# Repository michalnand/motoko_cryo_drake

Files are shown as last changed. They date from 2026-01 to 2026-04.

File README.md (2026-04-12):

# motoko cryo drake - line following robot

robot photos

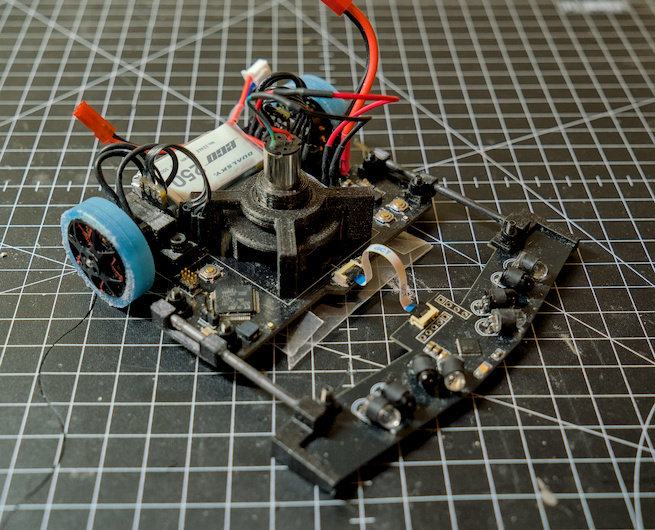
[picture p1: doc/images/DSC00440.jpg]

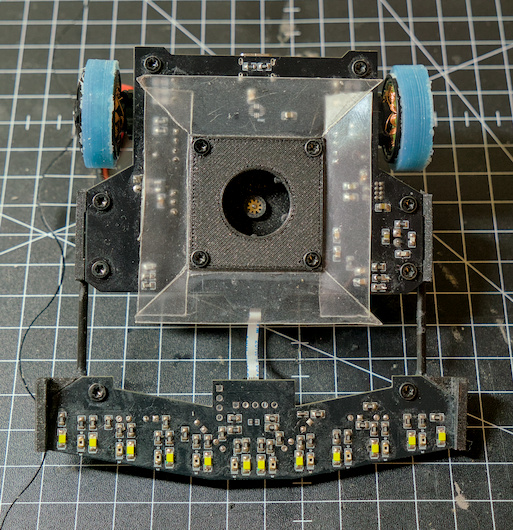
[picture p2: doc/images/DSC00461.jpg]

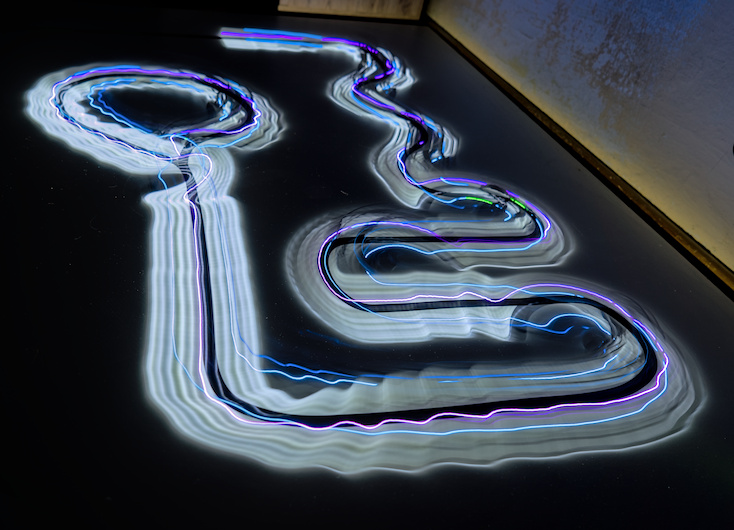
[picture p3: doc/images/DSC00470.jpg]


# hardware

- main MCU stm32f722, cortex m7, 216MHz, FPU
- sensors MCU stm32g031, cortex m0, 64MHz
- BLDC motors, custom windings, custom silicone tires
- 3 phase drivers, 2 x MP6541, 8A drivers
- turbine - some random DC drone motor + 3D print
- line sensors : 10x phototransistor + white LED
- obstacle sensors : 4x IR photo diode
- power 2D LiPo, Dualsky 250mAh
- USB C, debug connectors, RGB leds

# robot PCB

4 layer pcb, designed in EasyEDA

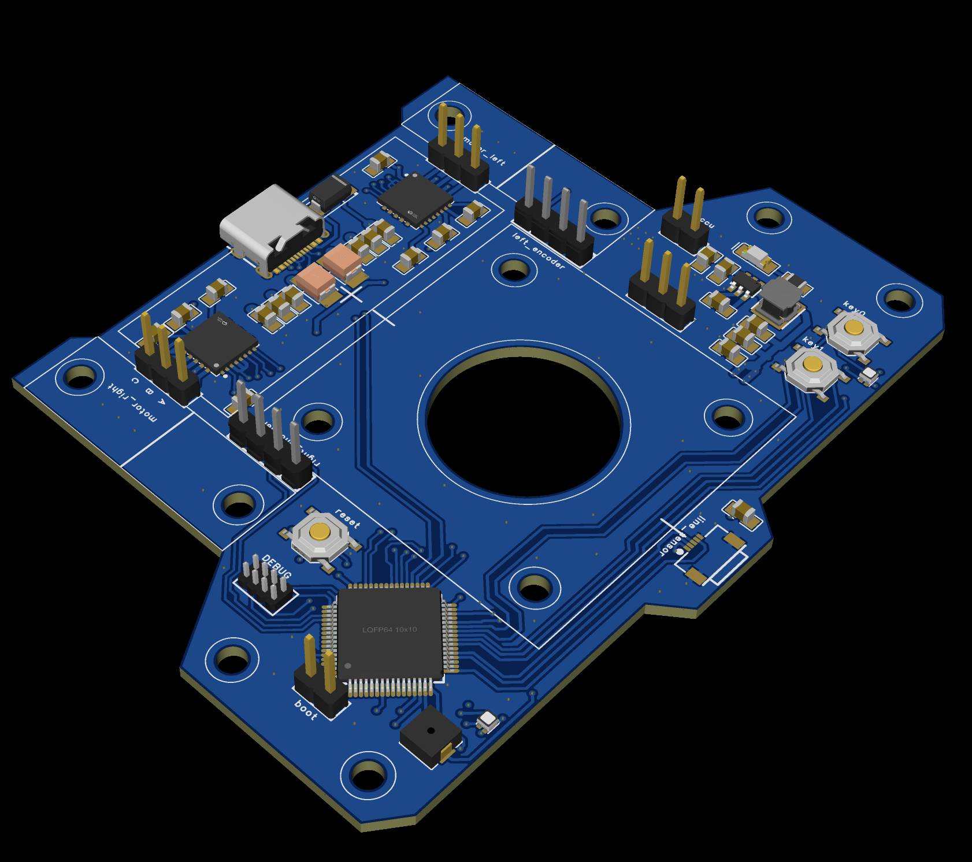
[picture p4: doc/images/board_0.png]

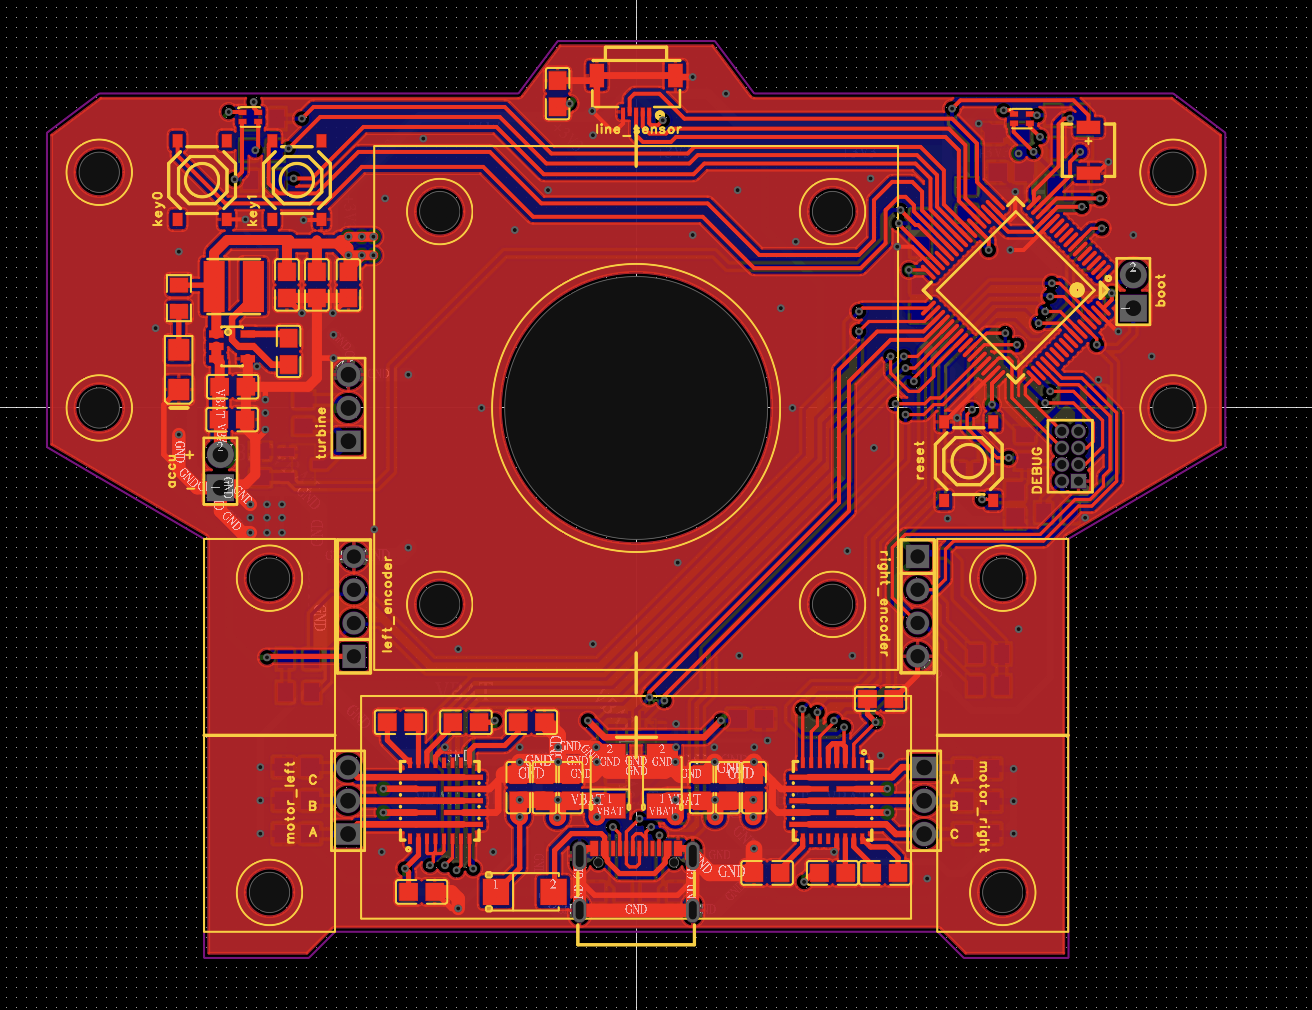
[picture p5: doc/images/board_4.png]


# software 

inner loop, 2kHz : 
- FOC control for BLDC motors
- kalman filter state estimator

outer loop
- analytical MPC
- constrained path planner
- koopman operator non linear controller

# block diagram

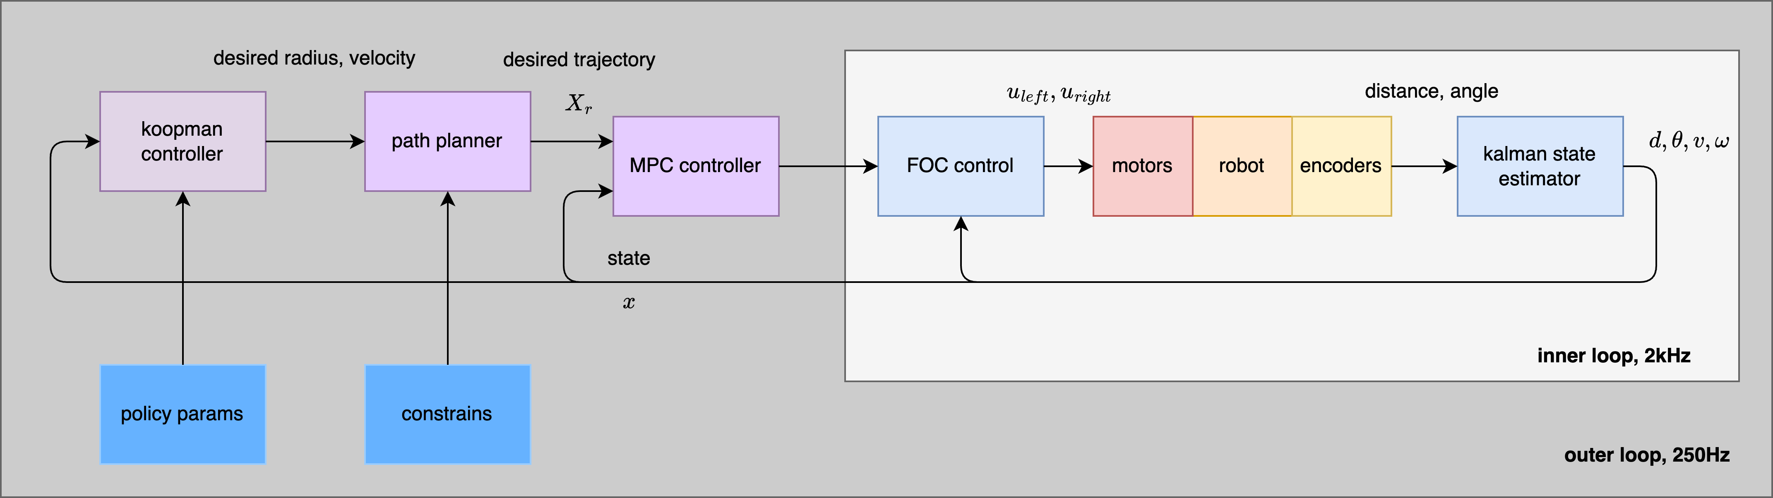
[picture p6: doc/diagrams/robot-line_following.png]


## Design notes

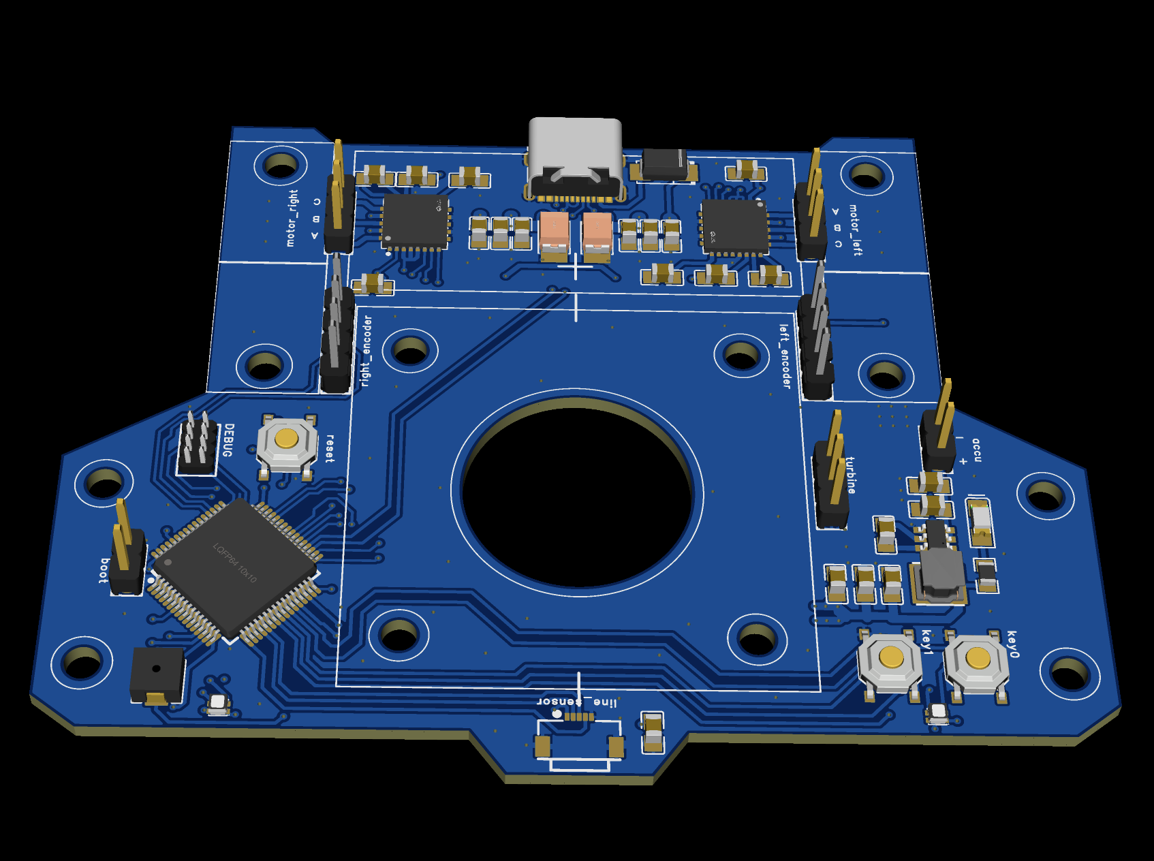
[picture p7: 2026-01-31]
doc/images/board_1.png

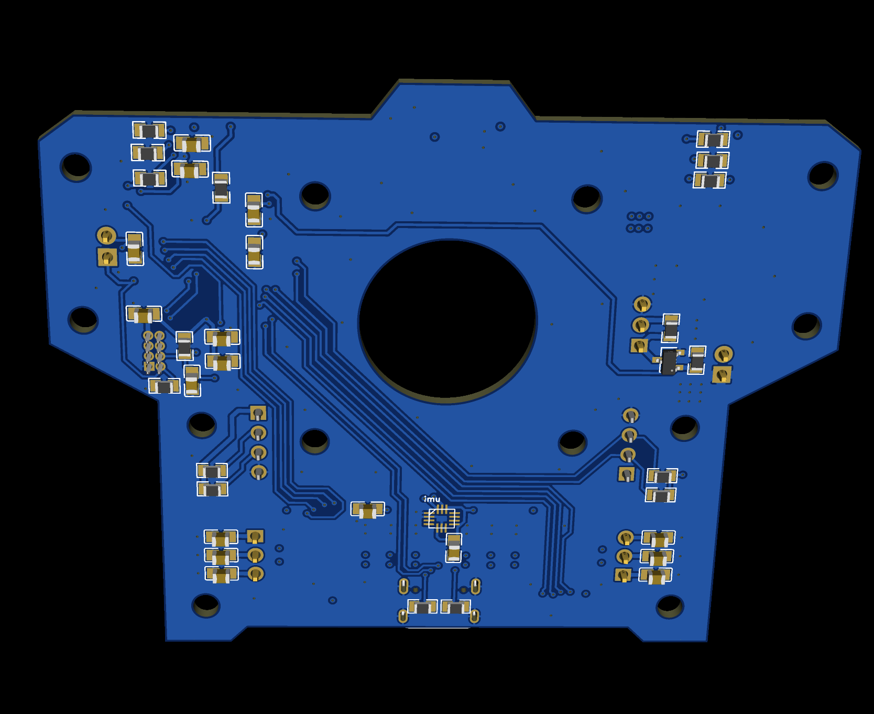
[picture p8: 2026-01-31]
doc/images/board_3.png

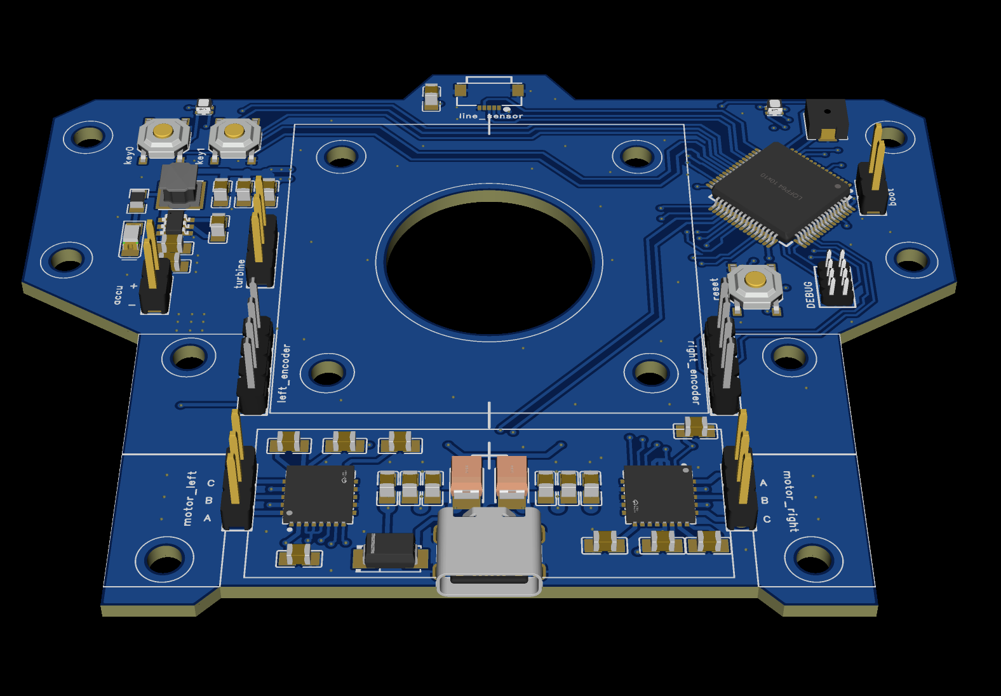
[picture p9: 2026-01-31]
doc/images/board_2.png

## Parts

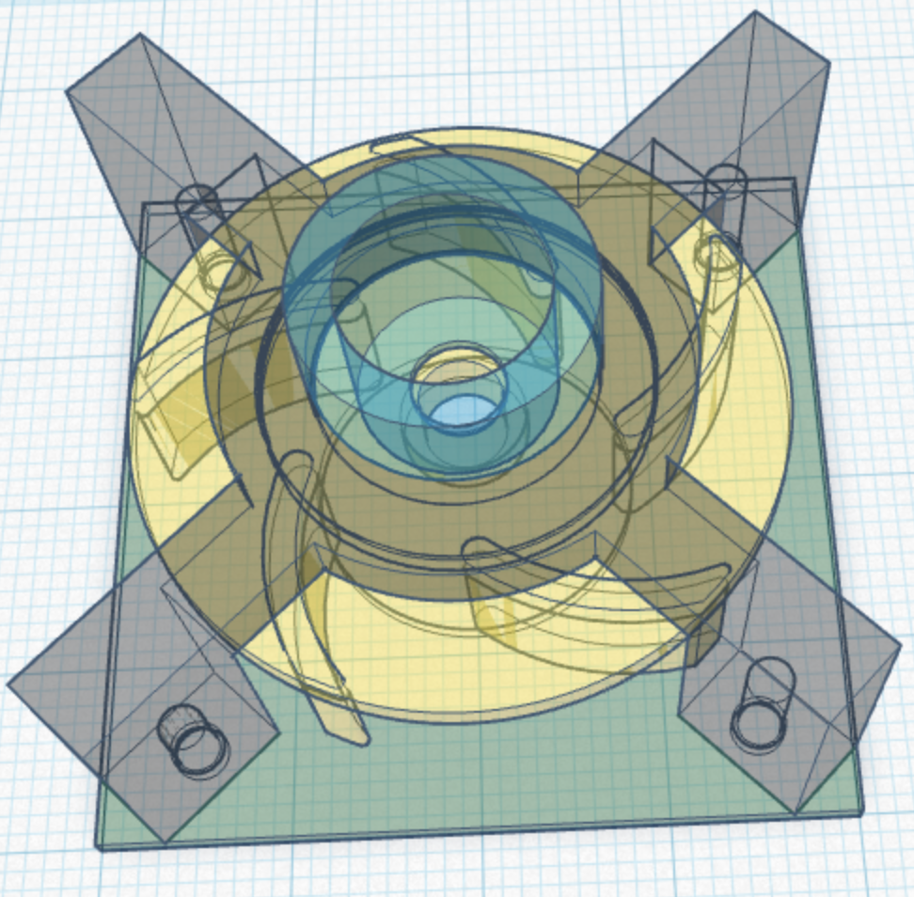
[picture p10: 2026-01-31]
3d_parts/images/turbofan.png

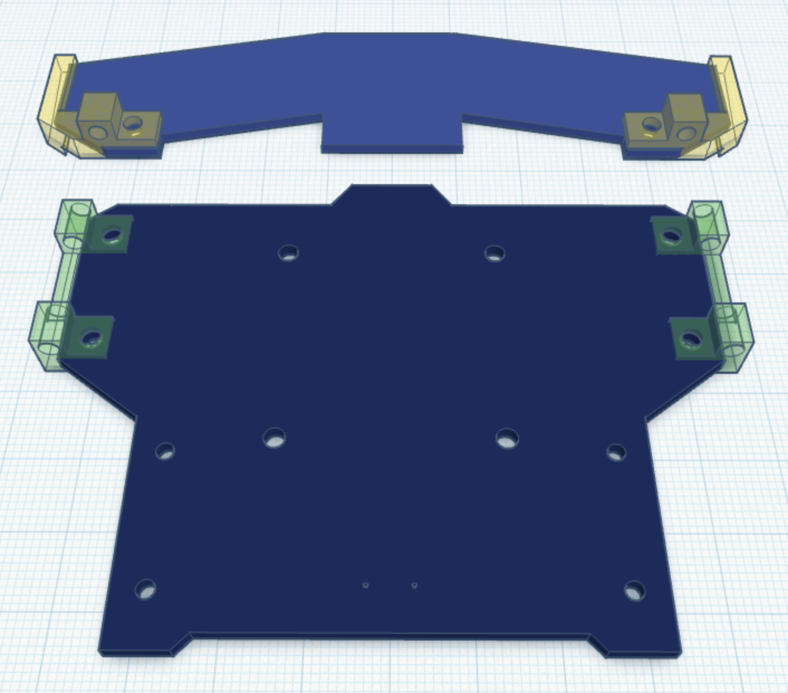
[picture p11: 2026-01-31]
3d_parts/images/sensor_holder_b.png

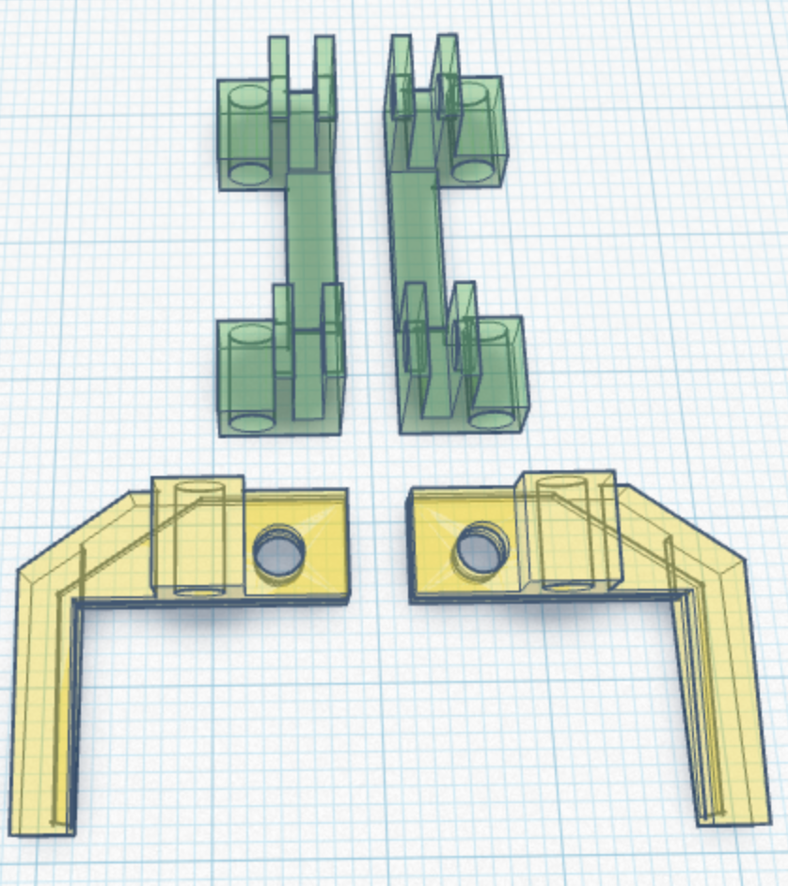
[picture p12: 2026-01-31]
3d_parts/images/sensor_holder_a.png

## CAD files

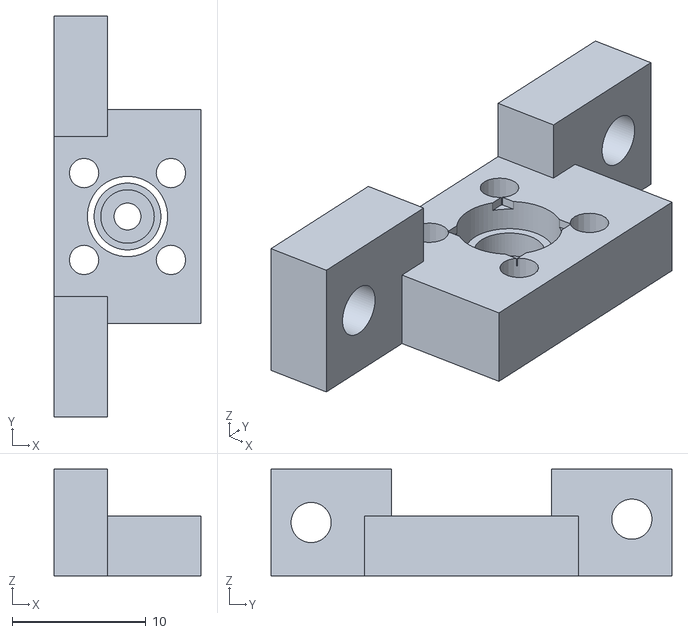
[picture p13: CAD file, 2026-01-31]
3d_parts/motors_bracket/motor_holder_1404.stl
11.0 x 30.0 x 8.00

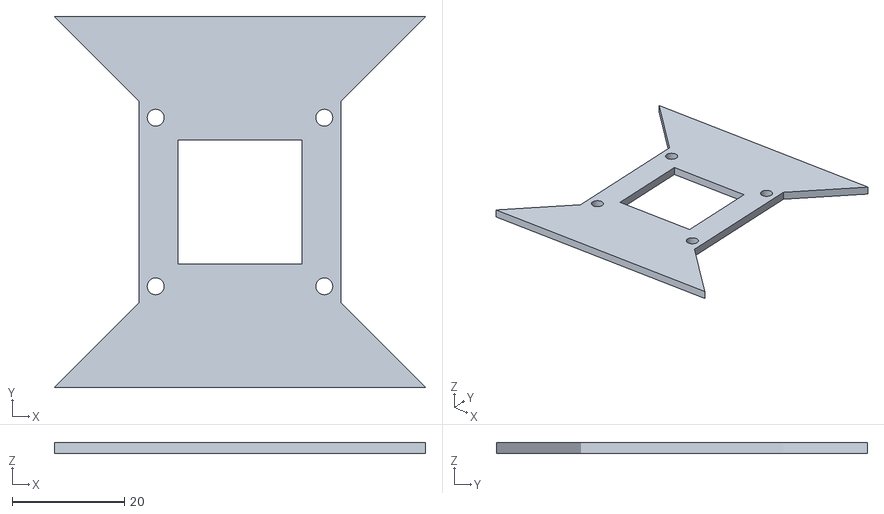
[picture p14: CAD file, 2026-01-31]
3d_parts/sealing_cut_jig/sealing_a.stl
66.0 x 66.0 x 2.00

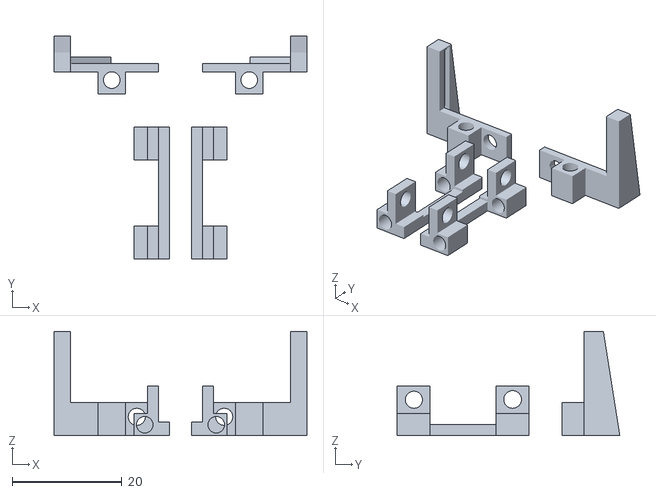
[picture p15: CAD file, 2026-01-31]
3d_parts/sensors/sensor_holder.stl
46.0 x 40.5 x 19.0

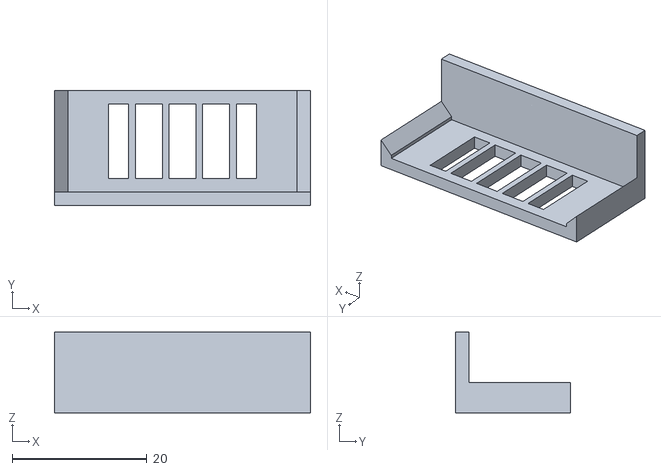
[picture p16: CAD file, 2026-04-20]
3d_parts/turbofan/turbo_fan_guard.stl
38.0 x 17.0 x 12.0

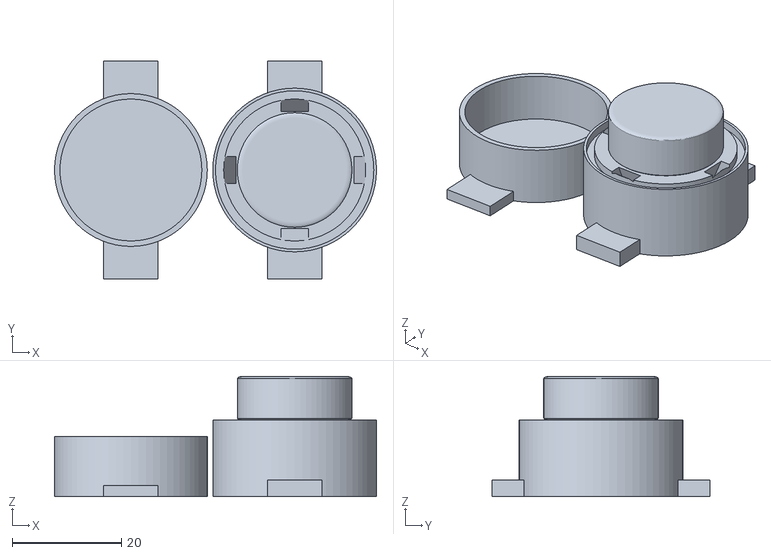
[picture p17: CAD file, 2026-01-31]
3d_parts/wheel_tire_silicone_form/whell_tire_form_b.stl
59.0 x 40.0 x 22.0

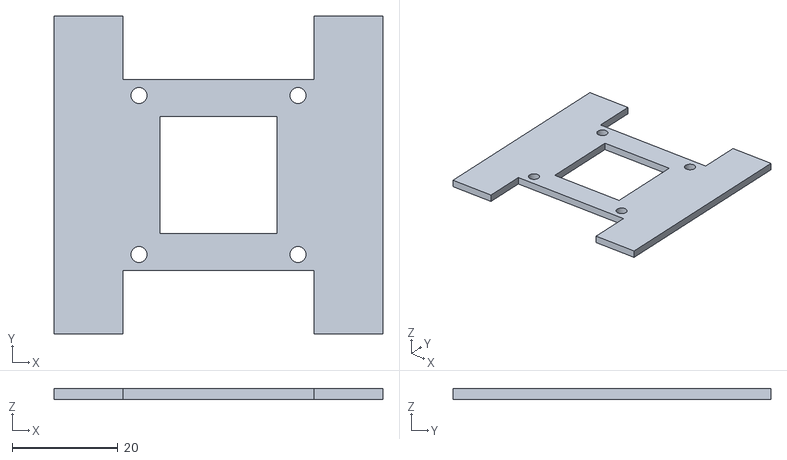
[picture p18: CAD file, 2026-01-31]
3d_parts/sealing_cut_jig/sealing_b.stl
62.0 x 60.0 x 2.00

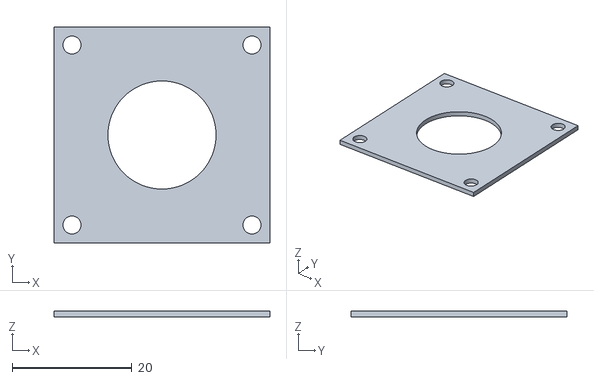
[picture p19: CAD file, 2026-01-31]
3d_parts/turbofan/turbofan_d.stl
36.0 x 36.0 x 1.00

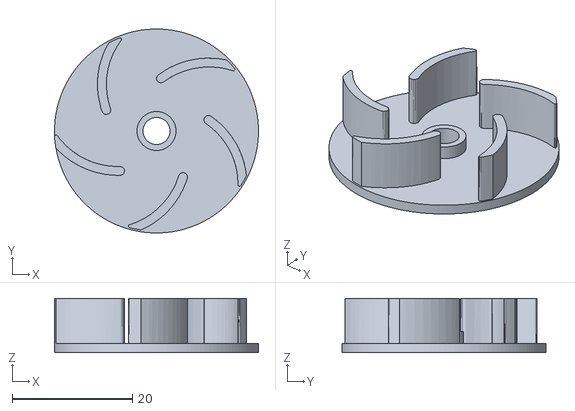
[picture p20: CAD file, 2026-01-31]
3d_parts/turbofan/turbofan_a.stl
34.0 x 34.0 x 9.01

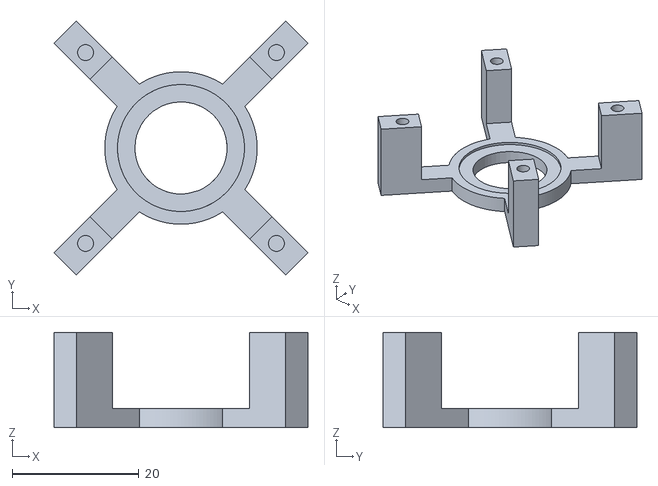
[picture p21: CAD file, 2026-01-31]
3d_parts/turbofan/turbofan_b.stl
40.0 x 40.0 x 15.0

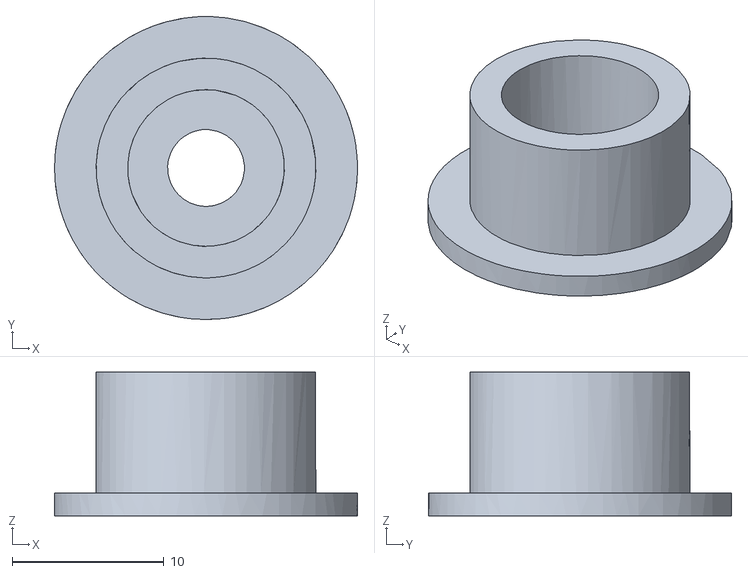
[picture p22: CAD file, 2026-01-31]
3d_parts/turbofan/turbofan_c.stl
20.0 x 20.0 x 9.50

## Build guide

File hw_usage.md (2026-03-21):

# STM32F722 Hardware Pin & Peripheral Usage

## Timers

| Timer / Source | Function | Frequency |
|---|---|---|
| SysTick | Timer, delays, basic timing | 1000 Hz |
| TIM7 (`TIM7_IRQHandler`) | Motor FOC control loop (incl. I2C encoder read) | 2000 Hz |
| TIM8/TIM13 (`TIM8_UP_TIM13_IRQHandler`) | Sensor sampling (line sensor, proximity) | 200 – 400 Hz |

---

## Turbine Fan PWM

| Signal | Pin  | Peripheral |
|---|---|---|
| PWM | PB10 | TIM2_CH3 |

---

## Left Motor – 3-Phase BLDC PWM (TIM3)

| Signal | Pin | Peripheral |
|---|-----|---|
| PWMA | PC6 | TIM3_CH1 |
| PWMB | PC7 | TIM3_CH2 |
| PWMC | PC8 | TIM3_CH3 |
| Enable | PC9 | GPIO |

## Right Motor – 3-Phase BLDC PWM (TIM4)

| Signal | Pin | Peripheral |
|---|-----|---|
| PWMA | PB6 | TIM4_CH1 |
| PWMB | PB7 | TIM4_CH2 |
| PWMC | PB8 | TIM4_CH3 |
| Enable | PB9 | GPIO |

---

## Motor Encoders (I2C, bit-bang)

| Encoder | SDA  | SCL  |
|---|---|---|
| Left encoder  | PC11 | PC10 |
| Right encoder | PB5  | PC12 |

---

## Line Sensor

| Signal | Pin | Type |
|---|-----|---|
| SDA | PA5 | I2C  |
| SCL | PA4 | I2C  |
| Reset  | PA3 | GPIO |

---

## Keys

| Key  | Pin |
|---|-----|
| KEY0 | PB2 |
| KEY1 | PB1 |

## RGB LEDs (active low)

| LED | R | G | B |
|---|-----|-----|-----|
| LED A | PB0 | PC4 | PA7 |
| LED B | PA0 | PA1 | PA2 |

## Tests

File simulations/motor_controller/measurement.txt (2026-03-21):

machine ready
u_in   =  0.200
k      =  321.474
rpm    = 613
x_mean =  64.294
x_var  =  48.687

u_in   =  0.300
k      =  273.746
rpm    = 784
x_mean =  82.124
x_var  =  78.852

u_in   =  0.400
k      =  230.747
rpm    = 881
x_mean =  92.298
x_var  =  145.622

u_in   =  0.500
k      =  198.342
rpm    = 947
x_mean =  99.171
x_var  =  108.676

u_in   =  0.600
k      =  175.433
rpm    = 1005
x_mean =  105.260
x_var  =  137.009

u_in   =  0.700
k      =  154.284
rpm    = 1031
x_mean =  107.999
x_var  =  169.827

u_in   =  0.800
k      =  139.777
rpm    = 1067
x_mean =  111.822
x_var  =  171.886

u_in   =  0.900
k      =  126.799
rpm    = 1089
x_mean =  114.119
x_var  =  154.503

u_in   =  1.000
k      =  116.872
rpm    = 1116
x_mean =  116.872
x_var  =  140.638

k          =  173.747
x_var_mean =  115.570

periods = 255
tau     =  7.321[ms]

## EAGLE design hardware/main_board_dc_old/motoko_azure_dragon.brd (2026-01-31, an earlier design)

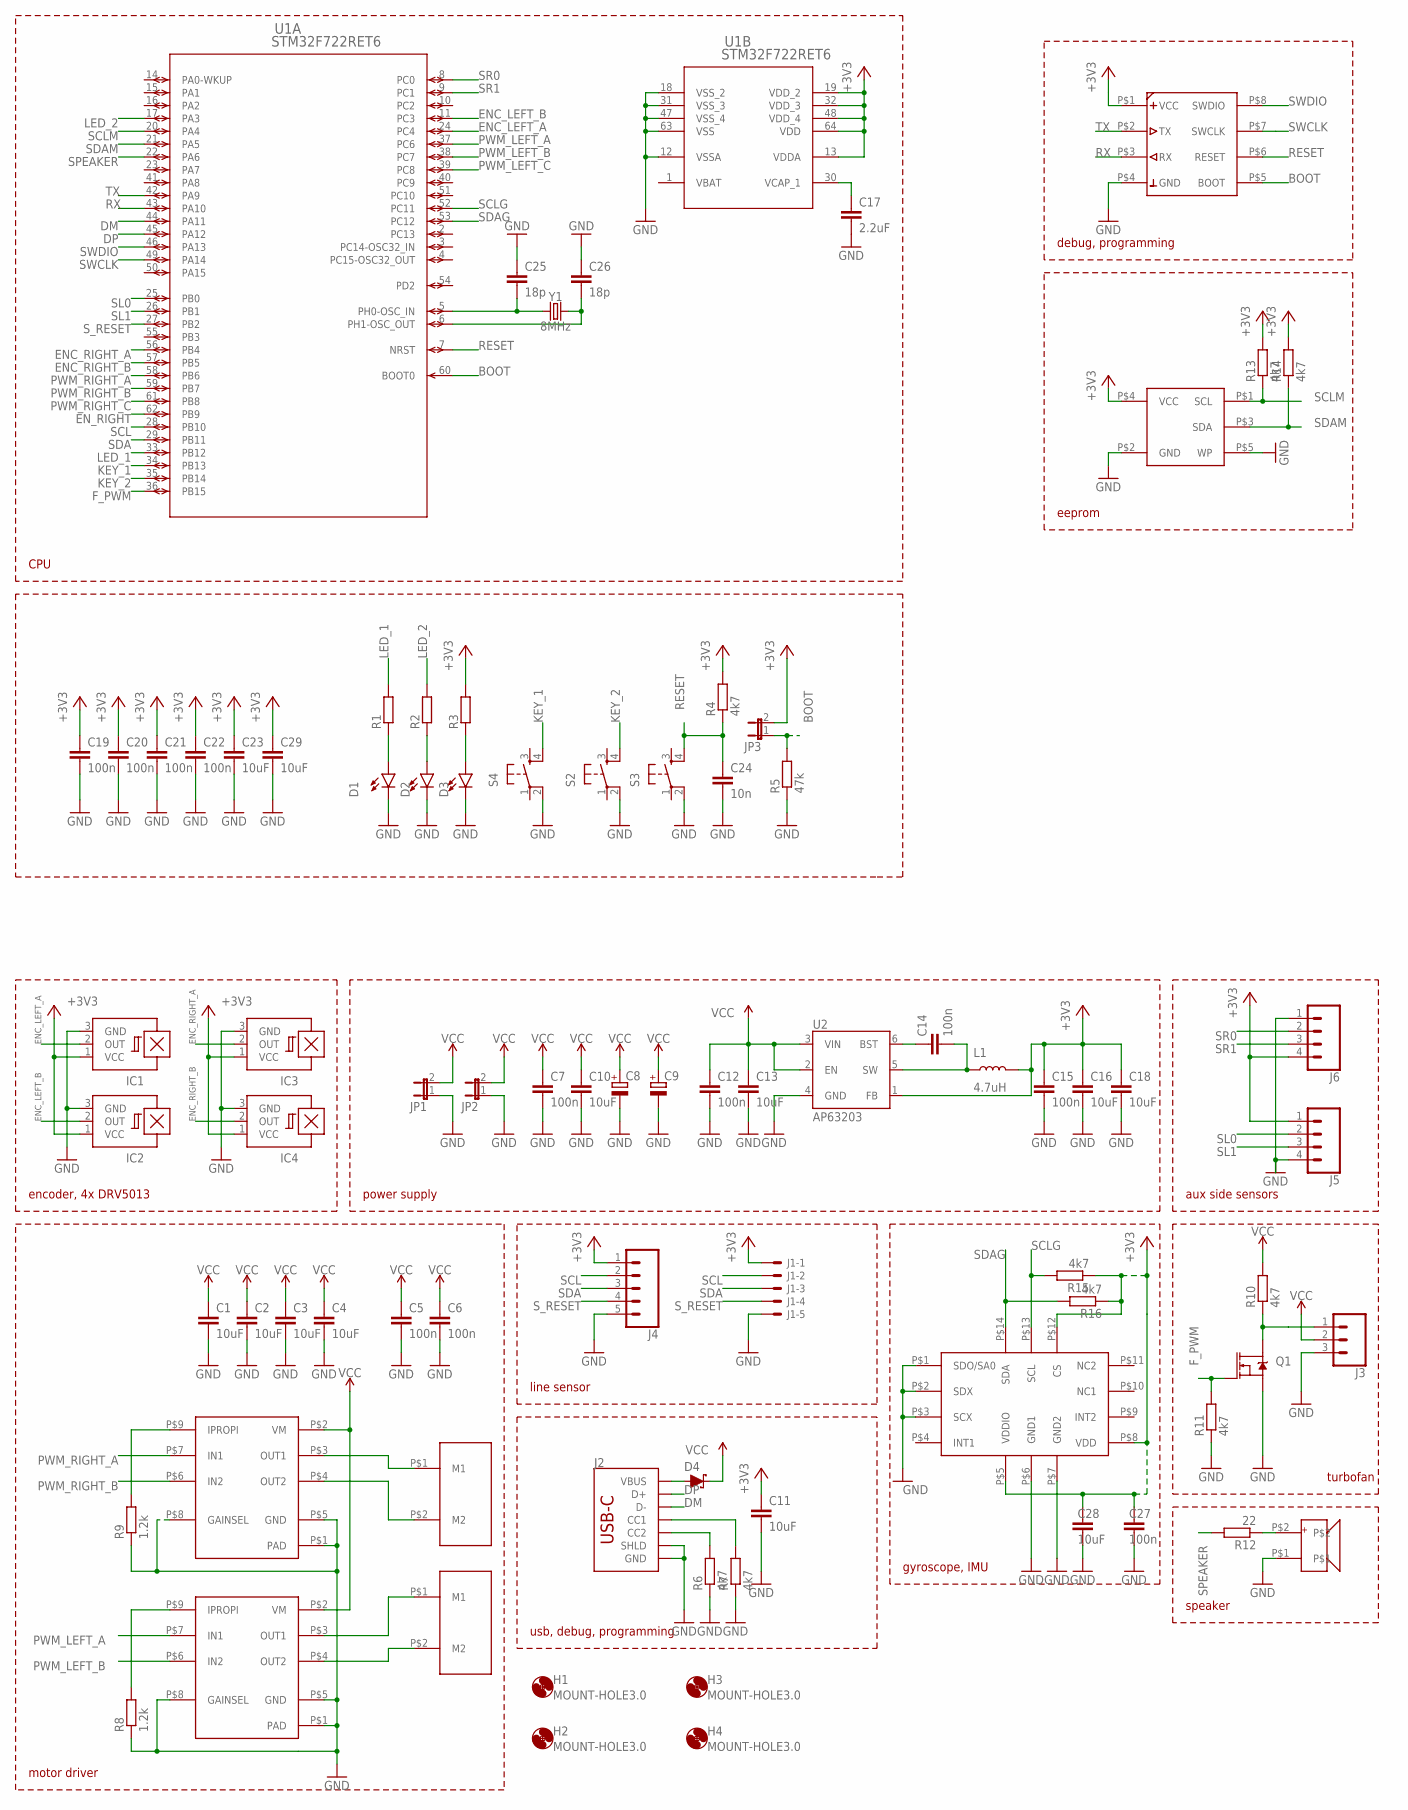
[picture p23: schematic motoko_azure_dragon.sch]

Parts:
C1, C2, C3, C4, C10, C11, C13, C16, C18, C23, C28, C29: 10uF; C0805
C5, C6, C7, C12, C14, C15, C19, C20, C21, C22, C27: 100n; C0805
C8, C9: CPOL-EUB/3528-21W; B/3528-21W
C17: 2.2uF; C0805
C24: 10n; C0805
C25, C26: 18p; C0805
D1, D2, D3: LED1206; LED-1206
D4: 3A/10V/280mV; SOD-323
H1, H2, H3, H4: MOUNT-HOLE3.0; 3,0
IC1, IC2, IC3, IC4: A1202LH; SOT23-W
J1: XF2L-0535-1
J2: USB_C_2-LAYER_PADS; USB-C-16P-2LAYER-PADS
J3: CONN_03LONGPADS; 1X03_LONGPADS
J4: CONN_051.27MM; 1X05_1.27MM
J5, J6: 1X04_SMD_STRAIGHT_COMBO; 1X04_SMD_VERTICAL_COMBO
JP1, JP2, JP3: JP1E; JP1
L1: 4.7uH; CR54
Q1: 5.8A/30V/35mΩ; SOT23-3
R1, R2, R3: R-EU_M0805; M0805
R4, R6, R7, R10, R11, R13, R14, R15, R16: 4k7; M0805
R5: 47k; M0805
R8, R9: 1.2k; M0805
R12: 22; M0805
S2, S3, S4: TAC_SWITCHSMD; TACTILE-SWITCH-SMD
U1: STM32F722RET6; LQFP64-10X10MM
U2: AP63203; SOT23-6
U$2, U$3: POLOLU_MICRO_METAL_GEAR_MOTOR
U$4, U$5: DRV8213; DSG8
U$6: 24LC24_SOT23; SOT23
U$7: DEBUG_CON; HEADER_4X2_1.27
U$8: LSM6DSM; LGA14L
U$9: SPEAKER_SMD_SMT0440
Y1: 8MHz; CRYSTAL-SMD-3.2X2.5MM

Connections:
+3V3: C11.1, C15.1, C16.1, C18.1, C19.1, C20.1, C21.1, C22.1, C23.1, C27.1, C28.1, C29.1, IC1.1 (VCC), IC2.1 (VCC), IC3.1 (VCC), IC4.1 (VCC), J1.1 (MSV), J4.1, J5.1, J6.4, JP3.2, L1.P$2 (2), R3.2, R4.2, R13.2, R14.2, R15.1, R16.1, U1.13 (VDDA), U1.19 (VDD_2), U1.32 (VDD_3), U1.48 (VDD_4), U1.64 (VDD), U2.1 (FB), U$6.P$4 (VCC), U$7.P$1 (VCC), U$8.P$5 (VDDIO), U$8.P$8 (VDD), U$8.P$12 (CS)
BOOT: JP3.1, R5.2, U1.60 (BOOT0), U$7.P$5 (BOOT)
DM: J2.A7 (D-), J2.B7 (D-), U1.44 (PA11)
DP: J2.A6 (D+), J2.B6 (D+), U1.45 (PA12)
ENC_LEFT_A: IC1.2 (OUT), U1.24 (PC4)
ENC_LEFT_B: IC2.2 (OUT), U1.11 (PC3)
ENC_RIGHT_A: IC3.2 (OUT), U1.56 (PB4)
ENC_RIGHT_B: IC4.2 (OUT), U1.57 (PB5)
EN_RIGHT: U1.62 (PB9)
F_PWM: Q1.1 (G), R11.2, U1.36 (PB15)
GND: C1.2, C2.2, C3.2, C4.2, C5.2, C6.2, C7.2, C8.-, C9.-, C10.2, C11.2, C12.2, C13.2, C15.2, C16.2, C17.2, C18.2, C19.2, C20.2, C21.2, C22.2, C23.2, C24.2, C25.1, C26.1, C27.2, C28.2, C29.2, D1.C, D2.C, D3.C, IC1.3 (GND), IC2.3 (GND), IC3.3 (GND), IC4.3 (GND), J1.5 (MS), J2.GND, J2.GND2 (GND), J2.SHLD1 (SHLD), J2.SHLD2 (SHLD), J2.SHLD3 (SHLD), J2.SHLD4 (SHLD), J3.3, J4.5, J5.4, J6.1, JP1.1, JP2.1, Q1.2 (S), R5.1, R6.1, R7.1, R8.1, R9.1, R11.1, S2.2, S3.2, S4.2, U1.12 (VSSA), U1.18 (VSS_2), U1.31 (VSS_3), U1.47 (VSS_4), U1.63 (VSS), U2.4 (GND), U$4.P$1 (PAD), U$4.P$5 (GND), U$4.P$8 (GAINSEL), U$5.P$1 (PAD), U$5.P$5 (GND), U$5.P$8 (GAINSEL), U$6.P$2 (GND), U$6.P$5 (WP), U$7.P$4 (GND), U$8.P$1 (SDO/SA0), U$8.P$2 (SDX), U$8.P$3 (SCX), U$8.P$6 (GND1), U$8.P$7 (GND2), U$9.P$1
KEY_1: S4.4, U1.34 (PB13)
KEY_2: S2.4, U1.35 (PB14)
LED_1: R1.2, U1.33 (PB12)
LED_2: R2.2, U1.17 (PA3)
unnamed: U$3.P$2 (M2), U$5.P$4 (OUT2)
unnamed: U$3.P$1 (M1), U$5.P$3 (OUT1)
unnamed: U$2.P$2 (M2), U$4.P$4 (OUT2)
unnamed: U$2.P$1 (M1), U$4.P$3 (OUT1)
unnamed: C14.2, L1.P$1 (1), U2.5 (SW)
unnamed: C14.1, U2.6 (BST)
unnamed: D1.A, R1.1
unnamed: D2.A, R2.1
unnamed: D3.A, R3.1
unnamed: J2.B5 (CC2), R6.2
unnamed: J2.A5 (CC1), R7.2
unnamed: C17.1, U1.30 (VCAP_1)
unnamed: C25.2, U1.5 (PH0-OSC_IN), Y1.1
unnamed: C26.2, U1.6 (PH1-OSC_OUT), Y1.3 (2)
unnamed: R8.2, U$5.P$9 (IPROPI)
unnamed: R9.2, U$4.P$9 (IPROPI)
unnamed: D4.A, J2.VBUS1 (VBUS), J2.VBUS2 (VBUS)
unnamed: J3.1, Q1.3 (D), R10.1
unnamed: R12.1, U$9.P$2
PWM_LEFT_A: U1.37 (PC6), U$5.P$7 (IN1)
PWM_LEFT_B: U1.38 (PC7), U$5.P$6 (IN2)
PWM_LEFT_C: U1.39 (PC8)
PWM_RIGHT_A: U1.58 (PB6), U$4.P$7 (IN1)
PWM_RIGHT_B: U1.59 (PB7), U$4.P$6 (IN2)
PWM_RIGHT_C: U1.61 (PB8)
RESET: C24.1, R4.1, S3.4, U1.7 (NRST), U$7.P$6 (RESET)
RX: U1.43 (PA10), U$7.P$3 (RX)
SCL: J1.2 (MS), J4.2, U1.28 (PB10)
SCLG: R15.2, U1.52 (PC11), U$8.P$13 (SCL)
SCLM: R13.1, U1.20 (PA4), U$6.P$1 (SCL)
SDA: J1.3 (MS), J4.3, U1.29 (PB11)
SDAG: R16.2, U1.53 (PC12), U$8.P$14 (SDA)
SDAM: R14.1, U1.21 (PA5), U$6.P$3 (SDA)
SL0: J5.2, U1.25 (PB0)
SL1: J5.3, U1.26 (PB1)
SPEAKER: R12.2, U1.22 (PA6)
SR0: J6.2, U1.8 (PC0)
SR1: J6.3, U1.9 (PC1)
SWCLK: U1.49 (PA14), U$7.P$7 (SWCLK)
SWDIO: U1.46 (PA13), U$7.P$8 (SWDIO)
S_RESET: J1.4 (MS), J4.4, U1.27 (PB2)
TX: U1.42 (PA9), U$7.P$2 (TX)
VBAT: U1.1 (VBAT)
VCC: C1.1, C2.1, C3.1, C4.1, C5.1, C6.1, C7.1, C8.+, C9.+, C10.1, C12.1, C13.1, D4.C, J3.2, JP1.2, JP2.2, R10.2, U2.2 (EN), U2.3 (VIN), U$4.P$2 (VM), U$5.P$2 (VM)

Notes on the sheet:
encoder, 4x DRV5013
motor driver
power supply
line sensor
aux side sensors
usb, debug, programming
turbofan
gyroscope, IMU
speaker
debug, programming
eeprom
CPU

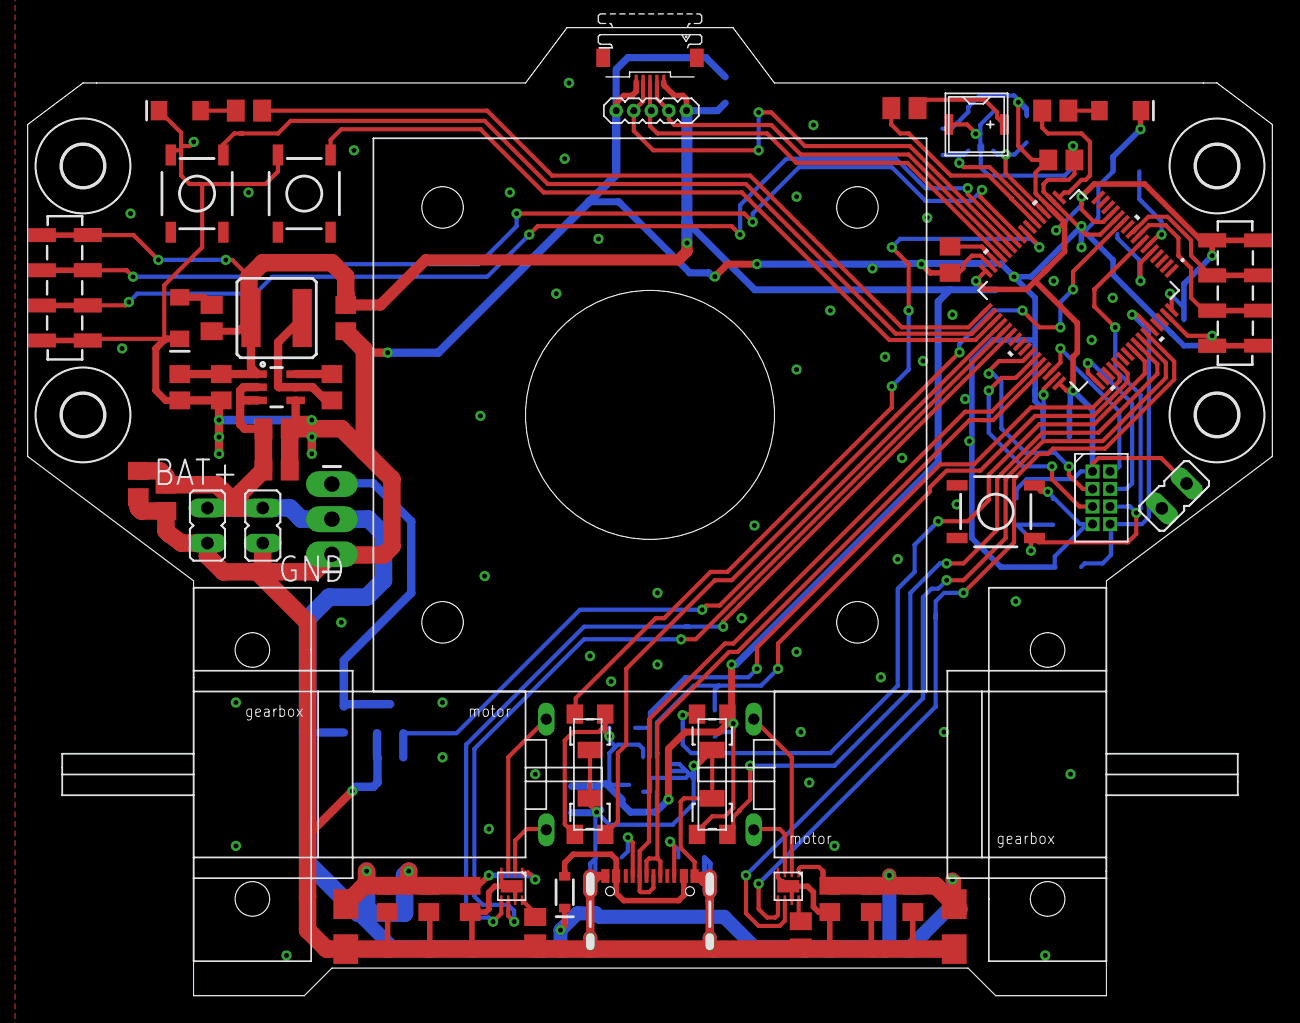
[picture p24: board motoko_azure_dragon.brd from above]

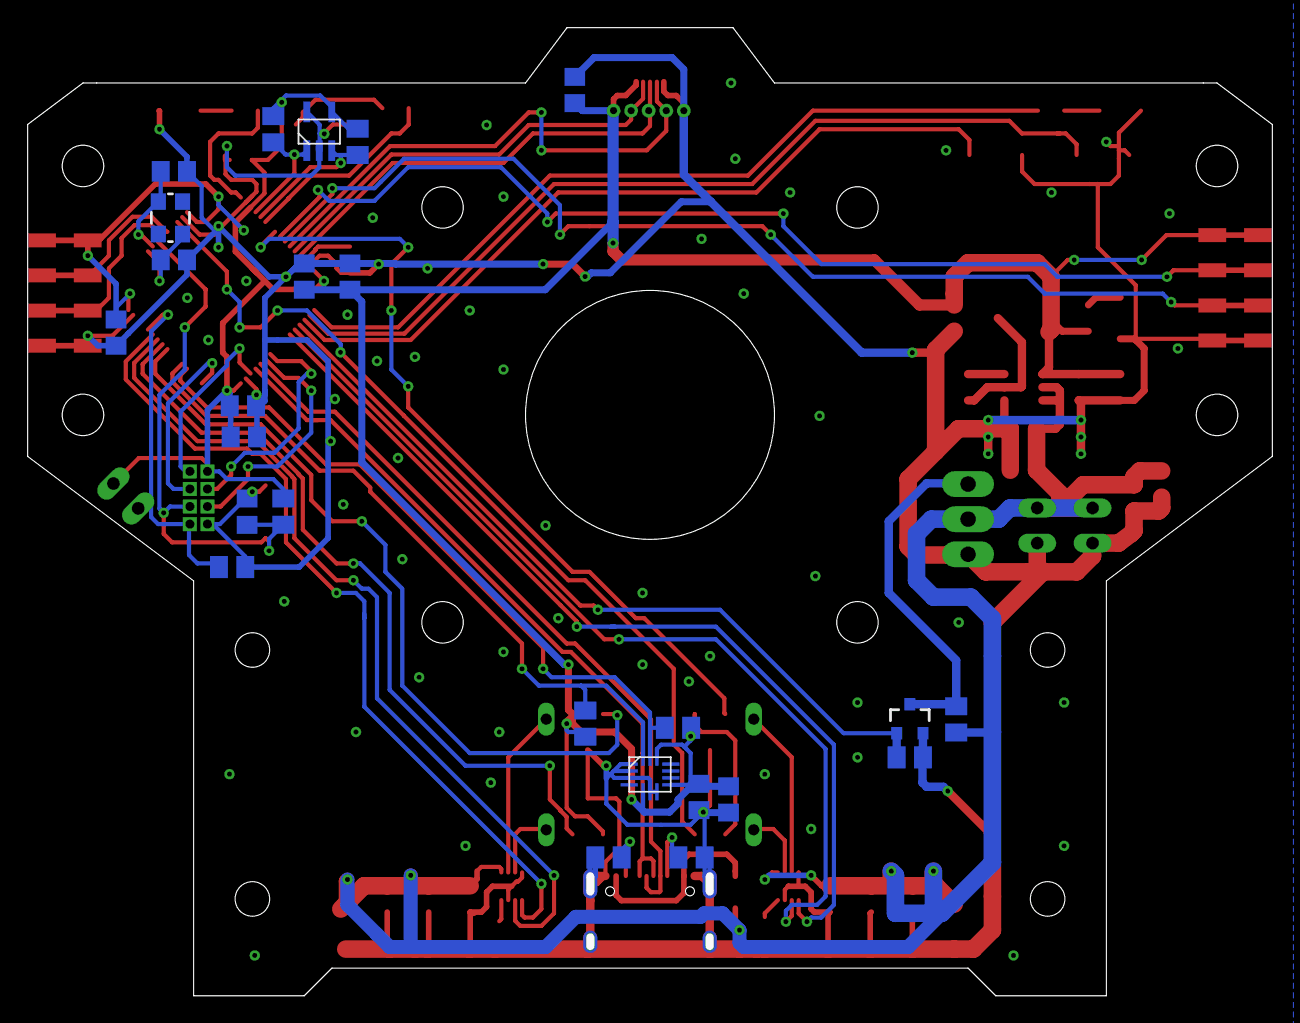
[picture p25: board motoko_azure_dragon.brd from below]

Board: 2 copper layers, 90.0 x 70.0 mm, 83 parts (25 on the bottom side), 55 nets.

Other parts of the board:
U$1: DUCTED_FAN_40MM

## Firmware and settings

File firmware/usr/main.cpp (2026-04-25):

#include "libs_drivers.h"
#include "tests.h"

#include "turbine.h"

#include "control_loop.h"

#include "line_follower.h"


int main()
{

    LibsDriversInit();

    terminal << "machine ready\n";

    
    
    LineFollower line_follower;
    line_follower.init(1);   
    key_wait();        

    line_follower.run();



    //motor_foc_test();

    //sensors_test();
    //encoder_test();   
    //motor_foc_test();

    //motor_identification();
    //motor_controll_test();    

    //robot_identification();    
    
    // init position control loop

    /*
    ControlLoop control_loop;
    control_loop.init();

    while (1) 
    {
        control_loop.set_position(0.0f, 0.0f*PI/180.0f);

        uint32_t steps_prev = control_loop.steps;
        timer.delay_ms(800);    
        uint32_t steps_curr = control_loop.steps;   

        uint32_t sps = (float)(steps_curr - steps_prev)*(1000.0f/800.0f);

        terminal << "sps "<< sps << "\n";   

        terminal << "distance "<< motor_control.state.x_dist_est*1000.0f << "\n";
        terminal << "angle    "<< motor_control.state.x_theta_est*180.0f/PI << "\n";    

        control_loop.set_position(0.0f, 90.0f*PI/180.0f);

        timer.delay_ms(800);  
        terminal << "distance "<< motor_control.state.x_dist_est*1000.0f << "\n";
        terminal << "angle "<< motor_control.state.x_theta_est*180.0f/PI << "\n"; 

        terminal << "\n\n"; 
    }
    */


    ControlLoop control_loop;
    control_loop.init();

    while (1)   
    {
        //control_loop.set_circle_motion(0.2f, 0.7f);
        control_loop.set_turn_motion(1.0f, 0.7f);
        timer.delay_ms(1000);      
        
        float turn_radius;

        turn_radius = motor_control.state.x_vel_est/motor_control.state.x_omega_est;
        
        terminal << "velocity " << motor_control.state.x_vel_est << "\n";
        terminal << "radius "   << turn_radius << "\n";
        terminal << "\n\n"; 
    }
    
    return 0;
}

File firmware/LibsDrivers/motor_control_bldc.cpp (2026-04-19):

#include <libs_drivers.h>
#include <motor_control_bldc.h>

#include <tmath.h>
#include <sine_table.h>
    
#define MOTOR_TIMER_FREQ             ((uint32_t)2000)
#define MOTOR_CONTROL_MAX_TORQUE     ((float)1.0)

    
#define MOTOR_POLES                  ((int32_t)14)       


#ifdef __cplusplus
extern "C" {
#endif

MotorControl *g_motor_control_ptr;

// timer 7 interrupt handler, running velocity control
void TIM7_IRQHandler(void)
{ 
    if (LL_TIM_IsActiveFlag_UPDATE(TIM7))
    {
        LL_TIM_ClearFlag_UPDATE(TIM7);
        g_motor_control_ptr->callback();
    }
}   


#ifdef __cplusplus
}
#endif


//init motor control process
int MotorControl::init(float k)
{
    g_motor_control_ptr = this;

    this->steps = 0;

    this->right_position = 0;
    this->left_position  = 0;


    this->right_torque        = 0;
    this->left_torque         = 0;

    this->right_velocity = 0;
    this->left_velocity  = 0;


    this->right_torque_s = 0;
    this->left_torque_s  = 0;

    this->left_cl_mode = false;
    this->right_cl_mode = false;

  
    this->k = k;
    
    
    right_pwm.init();
    left_pwm.init();    

    // set motors to zero position 
    for (unsigned int i = 0; i < 10; i++)     
    {
        int32_t torque = (PWM_VALUE_MAX*i)/10;
        set_torque_from_rotation(torque, (90*(int32_t)ENCODER_RESOLUTION)/360, 0);
        set_torque_from_rotation(torque, (90*(int32_t)ENCODER_RESOLUTION)/360, 1);
        timer.delay_ms(4);
    }

    
    timer.delay_ms(500);       

    // calibrate encoders   
    int right_init_res = right_encoder.init();   
    int left_init_res  = left_encoder.init(); 

    
    // release motors   
    set_torque_from_rotation(0, 0, 0);
    set_torque_from_rotation(0, 0, 1);

    timer.delay_ms(100);

    // velocity filters
    right_velocity_median_filter.init();
    left_velocity_median_filter.init();

    // state estimator, holds smooth robot state
    float pos_cutoff_freq = 200.0f;
    float vel_cutoff_freq = 200.0f;     
    state.init(pos_cutoff_freq, vel_cutoff_freq, 1.0f/MOTOR_TIMER_FREQ);


    // LQR + kalman init
    {
        float a =  0.93395853;
        float b =  11.47450799; 

        /*
        float k  =  0.00365991;
        float ki =  0.00030965;
        float f  =  0.08042387;
        */  

        float k  =  0.00064245;
        float ki =  4.45568037e-05;
        float f  =  0.08042387; 

        right_controller.init(a, b, k, ki, f, 1.0);
        left_controller.init(a, b, k, ki, f, 1.0);
    }



    //init timer  
    timer_init();

    if (left_init_res != 0)
    {
        return -1;
    }

    if (right_init_res != 0)
    {
        return -2;
    }

    return 0;
}


// range : -1, 1, for min and max torque
void  MotorControl::set_right_torque(float right_torque)
{
    this->right_cl_mode = false;
    this->right_torque  = right_torque;
    
}

// range : -1, 1, for min and max torque
void MotorControl::set_left_torque(float left_torque)
{
    this->left_cl_mode = false;
    this->left_torque   = left_torque;
}


// range : -1, 1, for min and max torque
void  MotorControl::set_right_velocity(float right_velocity)
{
    this->right_cl_mode = true;
    this->right_velocity  = right_velocity*MOTOR_CONTROL_MAX_VELOCITY;
    
}

// range : -1, 1, for min and max torque
void MotorControl::set_left_velocity(float left_velocity)
{
    this->left_cl_mode = true;
    this->left_velocity   = left_velocity*MOTOR_CONTROL_MAX_VELOCITY;
}   

void MotorControl::set(float forward, float turn)
{
    float right_torque = forward + turn;
    float left_torque  = forward - turn;

    set_right_torque(right_torque);
    set_left_torque(left_torque);
}   

// force break to both motors
void MotorControl::halt()
{
    set_torque_from_rotation(0, 0, 0);
    set_torque_from_rotation(0, 0, 1);
}

float MotorControl::get_right_position()
{
    return (2.0f*PI*right_encoder.position)/ENCODER_RESOLUTION;
}

float MotorControl::get_left_position()
{
    return -(2.0f*PI*left_encoder.position)/ENCODER_RESOLUTION;
}

void MotorControl::callback()
{
    // refresh encoders
    right_encoder.update();      
    left_encoder.update();          
    
    // update wheels state, position to radians
    float right_position        = (2.0f*PI*right_encoder.position)/ENCODER_RESOLUTION;
    float left_position         = -(2.0f*PI*left_encoder.position)/ENCODER_RESOLUTION;

    float right_velocity        = (right_position - this->right_position)/(1.0f/MOTOR_TIMER_FREQ);
    float left_velocity         = (left_position - this->left_position)/(1.0f/MOTOR_TIMER_FREQ);

    this->right_position = right_position;
    this->left_position  = left_position;
    
      
    // linear distance : average wheels traveled distance, convert radians to distance in meters
    float distance = 0.001*(WHEEL_RADIUS_MM)*(left_position + right_position)/(2.0f);

    // angle : difference of wheels traveled distance ratio to wheels brace, convert radians to angle
    float theta    = (WHEEL_RADIUS_MM)*(right_position - left_position)/(WHEEL_BRACE_MM);

    // update state estimator, holds smooth robot state
    state.step(distance, theta);     

    if (this->right_cl_mode)
    {
        this->right_torque_s = right_controller.step(this->right_velocity, right_velocity);
    }
    else
    {
        this->right_torque_s = this->k*this->right_torque_s + (1.0f - this->k)*this->right_torque;
        right_controller.kalman_step(right_velocity, this->right_torque_s);

    }

    if (this->left_cl_mode)
    {
        this->left_torque_s = left_controller.step(this->left_velocity, left_velocity);
    }
    else
    {
        this->left_torque_s = this->k*this->left_torque_s + (1.0f - this->k)*this->left_torque;
        left_controller.kalman_step(left_velocity, this->left_torque_s);
    }

    // scale -1...1 range into -PWM_VALUE_MAX .. PWM_VALUE_MAX
    // send torques to motors   
    set_torque_from_rotation(this->right_torque_s*PWM_VALUE_MAX, right_encoder.angle, 1);
    set_torque_from_rotation(-this->left_torque_s*PWM_VALUE_MAX, left_encoder.angle, 0);
    
        
    this->steps++;  
}









void MotorControl::timer_init()
{
    /* Enable TIM7 clock (on APB1) */
    LL_APB1_GRP1_EnableClock(LL_APB1_GRP1_PERIPH_TIM7);

    /* Disable TIM7 during configuration */
    LL_TIM_DisableCounter(TIM7);

    /* Timer clock = 216 MHz (APB1 doubled) */
    /* Prescaler = 215 → 216 MHz / 216 = 1 MHz timer tick */
    LL_TIM_SetPrescaler(TIM7, 215);

    /* Auto-reload for 4 kHz: 1 MHz / 250 = 4000 Hz */
    LL_TIM_SetAutoReload(TIM7, 1000000/MOTOR_TIMER_FREQ);


    /* Enable update interrupt (UIE) */
    LL_TIM_EnableIT_UPDATE(TIM7);       

    // TIM7  highest priority, preemption = 0   
    NVIC_SetPriority(TIM7_IRQn, NVIC_EncodePriority(0, 0, 0));
    NVIC_EnableIRQ(TIM7_IRQn);

    /* Clear update flag */
    LL_TIM_ClearFlag_UPDATE(TIM7);

    /* Start counter */
    LL_TIM_EnableCounter(TIM7);
}
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

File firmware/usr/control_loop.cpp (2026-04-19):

#include "control_loop.h"

#define CONTROLLER_UPDATE_RATE_HZ  ((uint32_t)250)

#ifdef __cplusplus  
extern "C" {    
#endif


ControlLoop *g_control_loop_ptr;

// timer 8 interrupt handler, running controller update
void TIM8_UP_TIM13_IRQHandler(void)
{ 
    if (LL_TIM_IsActiveFlag_UPDATE(TIM8))
    {
        LL_TIM_ClearFlag_UPDATE(TIM8);
        g_control_loop_ptr->callback();
    }
} 


#ifdef __cplusplus
}
#endif

int ControlLoop::init()
{
    // instance init, variables set
    g_control_loop_ptr = this;
    
    this->steps = 0;    

    this->r_min = 0.04f;
    this->r_max = 1.0f; 

    
    // shapers init, smooth run
    this->distance_target = 0.0f;
    this->angle_target    = 0.0f;
    this->radius_target   = 0.0f;
    this->velocity_target = 0.0f;

    
    this->position_mode = true;

    position_controller.init();

    
    this->timer_init();

    return 0;
}


void ControlLoop::set_position(float distance_target, float angle_target)
{
    this->distance_target = distance_target;
    this->angle_target    = angle_target;

    this->position_mode = true;
}

void ControlLoop::set_circle_motion(float radius_target, float velocity_target)
{
    this->velocity_target   = velocity_target;
    this->radius_target     = radius_target;

    this->position_mode = false;
}

void ControlLoop::set_turn_motion(float steering, float velocity_target)
{
    steering = clip(steering, -1.0f, 1.0f);     

    float k = abs(steering);
    float r = (1.0f - k)*this->r_max + k*this->r_min;

    r = sgn(steering)*r;      
    this->set_circle_motion(r, velocity_target);
}



void ControlLoop::callback()
{
    // udpate sensors data (line sensor, proximity sensor, incl filtering, processing)
    sensors.callback();

  
    // position control mode
    float acc_min   = -10.0f;    
    float acc_max   = 10.0f;    
    float acc_w_max = 100.0f;
    
    if (this->position_mode)
    {
        this->planner_set_position(this->distance_target, this->angle_target, acc_min, acc_max, acc_w_max);
    }
    else
    {
        this->planner_set_circle_motion(this->radius_target, this->velocity_target, acc_min, acc_max);
    }

    position_controller.callback(); 

    this->steps++;
}


/*
void ControlLoop::planner_set_position(float x_req, float a_req, float acc_min, float acc_max, float acc_w_max)
{
    // obtain time interval
    float dt = 1.0f/(float)CONTROLLER_UPDATE_RATE_HZ;

    // obtain state
    float x     = motor_control.state.x_dist_est;
    float v     = motor_control.state.x_vel_est;
    float a     = motor_control.state.x_theta_est;
    float w     = motor_control.state.x_omega_est;

    // required position change
    float v_req = (x_req - x)/dt;
    v_req       = v + clip((v_req - v), acc_min, acc_max);  

    // velocity braking limit 
    //float v_brake = sqrtf(2.0f * abs(acc_min) * abs(x_req - x)) * sgn(x_req - x);
    //v_req = sgn(v_req) * fminf(abs(v_req), abs(v_brake));
    
    float x_new = x + v_req*dt; 


    // required angle change
    float w_req = (a_req - a)/dt;   
    w_req       = w + clip((w_req - w), -acc_w_max, acc_w_max);
    float a_new = a + w_req*dt;

    position_controller.set_xr_constant(x_new, a_new);
}       
*/


void ControlLoop::planner_set_position(float x_req, float a_req, float acc_min, float acc_max, float acc_w_max)
{
    // obtain time interval
    float dt = 1.0f/(float)CONTROLLER_UPDATE_RATE_HZ;

    // obtain state
    float x     = motor_control.state.x_dist_est;
    float v     = motor_control.state.x_vel_est;
    float a     = motor_control.state.x_theta_est;
    float w     = motor_control.state.x_omega_est;

    float x_new, a_new;
    {
        float err = x_req - x;

        // max allowed position change this step
        float dx_max = 1.0 * dt;    

        // compute alpha so that:
        // alpha * err <= dx_max
        float alpha = abs(err) > 1e-2f ? min(1.0f, dx_max / abs(err)) : 1.0f;

        alpha = clip(alpha, 0.1f, 1.0f);
        x_new = (1.0f - alpha)*x + alpha*x_req;
    }

    {
        float err   = a_req - a;    
        float alpha = 1.0f/abs(0.1f*err);
        alpha = clip(alpha, 0.1f, 1.0f);
        a_new = (1.0f - alpha)*a + alpha*a_req;
    }

    position_controller.set_xr_constant(x_new, a_new);
} 



void ControlLoop::planner_set_circle_motion(float r_req, float v_req, float acc_min, float acc_max)
{
    // obtain time interval
    float dt = 1.0f/(float)CONTROLLER_UPDATE_RATE_HZ;

    // obtain state
    float x     = motor_control.state.x_dist_est;
    float v     = motor_control.state.x_vel_est;
    float a     = motor_control.state.x_theta_est;
    float w     = motor_control.state.x_omega_est;


    // estimate required velocity change (acceleration)
    float acc_req = (v_req - v)/dt;

    // acceleration limit
    acc_req = clip(acc_req, acc_min, acc_max);

    float v_curr    = v;
    float req_x     = x;
    float req_angle = a;

    float r_req_safe = sgn(r_req)*max(abs(r_req), 0.01f);

    
    for (unsigned int n = 0; n < MPC_PREDCTION_HORIZON; n++)
    {
        // update velocity with acceleration, and constrains
        v_curr+= acc_req*dt;
        v_curr = clip(v_curr, -abs(v_req), abs(v_req)); 

        //split velocity to tangential and angular components
        float vc = v_curr;  
        float va = v_curr/r_req_safe;    
        
        // calculate motion change
        req_x+= vc*2.5f*dt;     
        req_angle+= va*dt;         

        // fill controller predictive trajectory with calculated motion change
        this->position_controller.set_xr_trajectory(n, req_x, req_angle);
    }
    

    /*
    // update velocity with acceleration, and constrains
    v_curr+= acc_req*dt;
    v_curr = clip(v_curr, -abs(v_req), abs(v_req)); 

    //split velocity to tangential and angular components
    float vc = v_curr;  
    float va = v_curr/r_req_safe;    
    
    // calculate motion change
    req_x+= vc*dt;
    req_angle+= va*dt;      

    // fill controller predictive trajectory with calculated motion change
    this->position_controller.set_xr_constant(req_x, req_angle);
    */
}

float ControlLoop::get_distance()
{
    return motor_control.state.x_dist_est;
}

float ControlLoop::get_angle()
{
    return motor_control.state.x_theta_est;
}

float ControlLoop::get_velocity()
{
    return motor_control.state.x_vel_est;
}

float ControlLoop::get_angular_velocity()
{
    return motor_control.state.x_omega_est;
}
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

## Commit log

2026-03-10 sensors tested + driver, FOC for motors + encoders tests, open loop control
2026-03-11 motor identification
2026-03-11 motor controller + state estimator
    [measured.csv]
2026-03-19 identification fix + lqr fix
    [control_loop.cpp, main.cpp, motor_control_bldc.cpp]
2026-03-20 mpc controller
    [measured.csv]
2026-04-11 broken line, params tunned
    [control_loop.cpp, main.cpp, sensors.cpp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]
2026-04-12 proximity sensors calibration
2026-04-13 obstacle avoid, not tested
    [sensors.cpp, sensors.h]
2026-04-20 something is working
    [turbo_fan_guard.stl]

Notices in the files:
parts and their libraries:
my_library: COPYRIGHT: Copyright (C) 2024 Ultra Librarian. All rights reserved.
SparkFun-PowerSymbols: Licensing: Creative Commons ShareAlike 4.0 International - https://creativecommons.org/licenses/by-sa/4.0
